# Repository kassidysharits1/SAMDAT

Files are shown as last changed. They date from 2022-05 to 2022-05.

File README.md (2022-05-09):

# SAMDAT


The goal of this project is to create a semi-autonomous magnetics data acquisition tool (SAMDAT). The use of a semi-autonomous vehicle for geophysical data acquisition yields the possibility for quick and efficient surveying. We see rovers being used on other planets, however in the geophysics industry on Earth this is not seen often. This project will aim to create a semi- autonomous tool to collect magnetic data. The goal is for the final product to be relatively low cost and to hopefully have the ability to be used for other geophysical applications with a selection of sensors. 

# Equipment
- Magnetic Fluxgate (https://www.mouser.com/ProductDetail/Texas-Instruments/DRV425EVM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) 
- GPS (https://www.openimpulse.com/blog/products-page/product-category/gy-neo6mv2-gps-module/) 
- Robotics Kits Robot Car Kit-6WD Off-Road Chassis (https://www.electromaker.io/shop/product/robot-car-kit-6wd-off-road-chassis) 
- Arduino Mega 2560 (2) (https://store-usa.arduino.cc/products/arduino-mega-2560-rev3?selectedStore=us)
- Ethernet Shield (https://www.amazon.com/SunFounder-Ethernet-Shield-W5100-Arduino/dp/B00HG82V1A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)
- Micro SD
- Bluetooth (https://makersportal.com/blog/2017/9/20/hm-10-bluetooth-module)
- Motor Driver (2-3) (https://create.arduino.cc/projecthub/ryanchan/how-to-use-the-l298n-motor-driver-b124c5)
- Battery to power car (https://hobbyking.com/en_us/turnigy-5000mah-3s-20c-lipo-pack-xt-90.html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)
- 9V batteries for arduinos 
- Connectors for batteries, arduinos, sensors
- 3D printed magnetometer extender 

# Estimated Cost Analysis:
Below lists the approximated cost of equipment, this parts list assumes buying one sensor as opposed to discounted builk deliveries and does not include tax and shipping. Note that we bought the sensors and arduinos in bulk and therefore our project was a bit less than this cost analysis.
- Robotics Kit: $99.90
- Magnetic Fluxgate: $24
- Arduino Mega: $35.93 (2)
- Ethernet Shield: $20.99
- Micro SD Card: $9
- Motor Driver: $6.99 (3)
- 14.8 V Lithium Ion Battery: $20.89
- 9V batteries: $2 (2)
- GPS Module: $10
- HM10 Bluetooth Module: $10.99

Total: $292.60

# Design
### Robotic Car Kit
Youtube video linked below with a walk through assembly for the 6 WD High Speed Crawler Robot Chassis with Suspension:
https://www.youtube.com/watch?v=SU6XHG54L_c 

Building guide linked below with equipment and build pictures:
https://raw.githubusercontent.com/SeeedDocument/Outsourcing/master/6WD/Robot%20Car%20Kit-6WD%20Off-Road%20Chassis%20Kit%20Guide%20EN%20V1.0.pdf 

### Motor Driver
Note that we are not using a 9V battery, the battery to power the car is being used here.
driver
Figure: Schematic of motor driver

### Magnetic Fluxgate 
Connections: 
- top connection goes to REFOUT
- second connection goes to VOUT
- third connection goes to ground
- fourth connection not used
mag_img
Figure: Magnetic Fluxgate Top View
diagram_mag
Figure: Schematic of Magnetic Fluxgate

### Attaching the magnetometer at a safe distance
Because the robotic car and the arduinos are magnetic, the magnetic fluxgate needs to be suspended a safe distance from this equipment so that it does not pick up these magnetic anomalies and thus recording false anomalies. This was accounted for by 3D-printing a small rod that can be attached to the robotic car platform and extends roughly 5 inches out. We completed some testing with the magnetic fluxgate and the platform and found that magnetic fluxgate reports steady values once it is 5 inches away from the platform. We tested this while running the motor since this does produce a slightly larger anomaly. We decided to give 10 inches for extra measure. 

https://user-images.githubusercontent.com/103535565/163262615-a055875f-b65d-4c38-8e55-ccc3797bc589.MOV

### Bluetooth
hm10

### 3D Printed Magnetometer Extender
The solid works file for this project are attached in this github directory. 

## Compilation
The following diagrams show the wiring diagrams for the driving and data collection systems. Note that the pin connection locations in the diagrams do not align with our project as the diagrams are drawn with an Arduino Uno rather than a Arduino Mega 2560.

### Rover Driving System
Driving System Diagram

### Data Collection System
Data Collection System Diagram

# Test Survey
This video shows the SAMDAT in action in a hallway running over a series of fridge magnets.

https://user-images.githubusercontent.com/104784140/167321360-39053b76-8c38-48cc-887e-6265c37ef1ad.mp4

# Video
Below shows a video of SAMDAT in action on the Colorado School of Mines campus. 

https://user-images.githubusercontent.com/103535565/165623426-cf573f2c-155d-4962-ba4c-ab2bb2be90a3.mov

# Improvements and Potentials
There is large potential with this project to be applied to other geophysical problems using various sensors. By making interchangeable attachments, there is the potential to use other geophysical equipment. The 3D printed rod we attached for the magnetometer is removable and could be replaced with an attached cart that can hold various equipment. 

Specific Recommended improvements:

- Add a surveyor's wheel for better distance precision/accuracy
- Add fifth and sixth wheels to driving system
- Improve weight distribution: the rover currently drives slightly crooked because the weight is not distributed evenly (mainly the heavy battery causing these issues).
- Adaptive driving from GPS information paired with wheel position sensors.
- Waterproofing for all weather conditions.

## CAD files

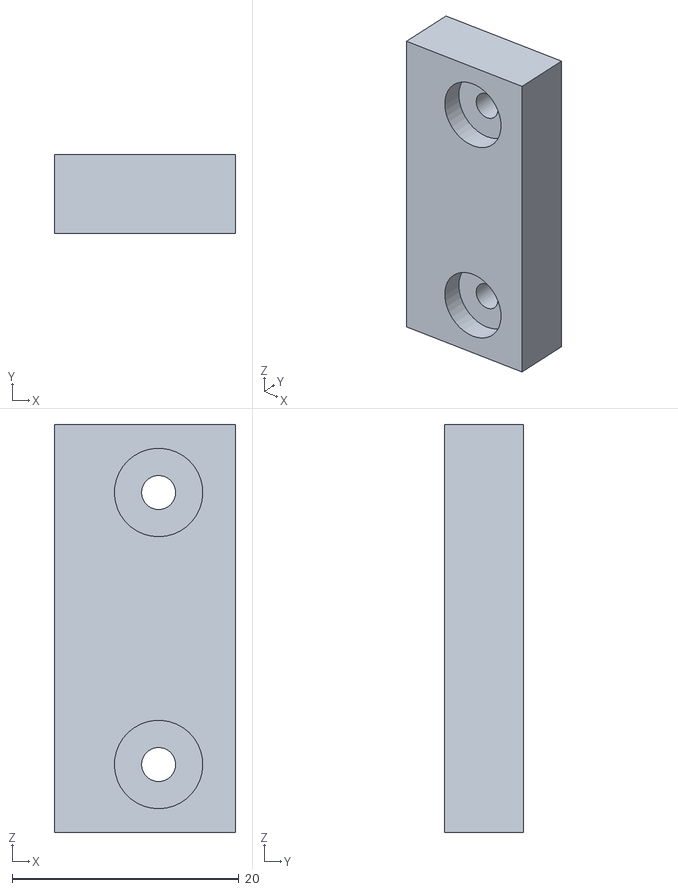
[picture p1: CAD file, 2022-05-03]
bottomclamp.STL
16.0 x 7.00 x 36.0

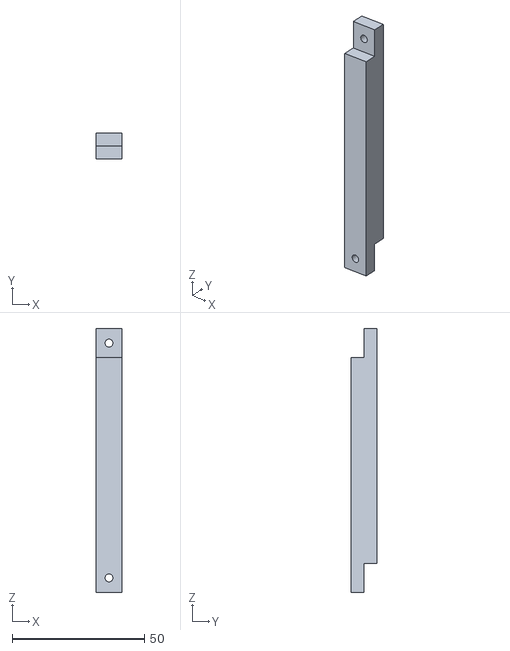
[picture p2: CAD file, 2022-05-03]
arm_10cm.STL
9.80 x 10.0 x 100.0

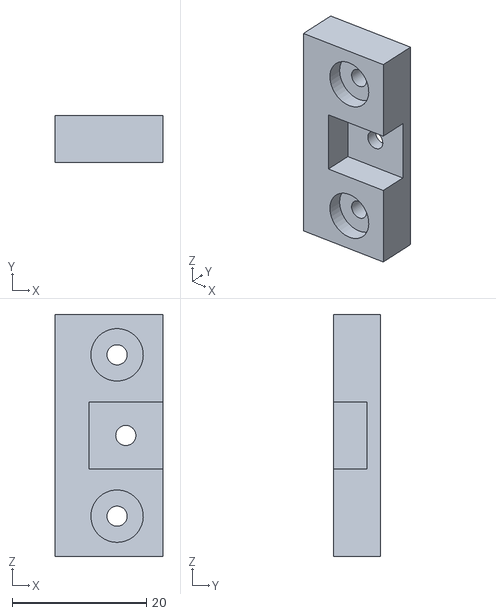
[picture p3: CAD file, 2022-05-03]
topclamp.STL
16.0 x 7.00 x 36.0

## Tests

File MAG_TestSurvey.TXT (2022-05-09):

FieldStrength(nT), Satellites, HDOP, Latitude(deg), Longitude(deg), Fix, Altitude(m), Hour, Minute, Second, Centisecond, day, month, year
----------------------------------------------------------------------------------------------------------------------------------------------
52151.64,0,0,0.00,0.00,4294967295,0.00,0,0,0,0,0,0,2000
52151.64,0,0,0.00,0.00,4294967295,0.00,0,0,0,0,0,0,2000
52049.18,0,9999,0.00,0.00,4294967295,0.00,0,0,0,0,0,0,2000
52151.64,0,9999,0.00,0.00,4294967295,0.00,0,0,0,0,0,0,2000
52049.18,0,9999,0.00,0.00,4294967295,0.00,0,0,0,0,0,0,2000
52049.18,0,9999,0.00,0.00,4294967295,0.00,0,0,0,0,0,0,2000
52151.64,0,9999,0.00,0.00,4294967295,0.00,0,0,0,0,0,0,2000
52151.64,0,9999,0.00,0.00,4294967295,0.00,0,0,0,0,0,0,2000
52151.64,0,9999,0.00,0.00,4294967295,0.00,0,0,0,0,0,0,2000
52151.64,0,9999,0.00,0.00,4294967295,0.00,0,0,0,0,0,0,2000
52151.64,0,9999,0.00,0.00,4294967295,0.00,0,0,0,0,0,0,2000
52049.18,0,9999,0.00,0.00,4294967295,0.00,0,0,0,0,0,0,2000
52049.18,0,9999,0.00,0.00,4294967295,0.00,0,0,0,0,0,0,2000
52049.18,0,9999,0.00,0.00,4294967295,0.00,0,0,0,0,0,0,2000
52151.64,0,9999,0.00,0.00,4294967295,0.00,0,0,0,0,0,0,2000
52151.64,0,9999,0.00,0.00,4294967295,0.00,0,0,0,0,0,0,2000
52151.64,0,9999,0.00,0.00,4294967295,0.00,0,0,0,0,0,0,2000
52151.64,0,9999,0.00,0.00,4294967295,0.00,0,0,0,0,0,0,2000
52151.64,0,9999,0.00,0.00,4294967295,0.00,0,0,0,0,0,0,2000
52151.64,0,9999,0.00,0.00,4294967295,0.00,0,0,0,0,0,0,2000
52151.64,0,9999,0.00,0.00,4294967295,0.00,0,0,0,0,0,0,2000
52049.18,0,9999,0.00,0.00,4294967295,0.00,0,0,0,0,0,0,2000
52254.10,0,9999,0.00,0.00,4294967295,0.00,0,0,0,0,0,0,2000
52049.18,0,9999,0.00,0.00,4294967295,0.00,0,0,0,0,0,0,2000
52151.64,0,9999,0.00,0.00,4294967295,0.00,0,0,0,0,0,0,2000
52356.55,0,9999,0.00,0.00,4294967295,0.00,0,0,0,0,0,0,2000
52459.01,0,9999,0.00,0.00,4294967295,0.00,0,0,0,0,0,0,2000
52561.48,0,9999,0.00,0.00,4294967295,0.00,0,0,0,0,0,0,2000
52561.48,0,9999,0.00,0.00,4294967295,0.00,0,0,0,0,0,0,2000
52459.01,0,9999,0.00,0.00,4294967295,0.00,0,0,0,0,0,0,2000
52356.55,0,9999,0.00,0.00,4294967295,0.00,0,0,0,0,0,0,2000
52356.55,0,9999,0.00,0.00,4294967295,0.00,0,0,0,0,0,0,2000
52356.55,0,9999,0.00,0.00,4294967295,0.00,0,0,0,0,0,0,2000
52356.55,0,9999,0.00,0.00,4294967295,0.00,0,0,0,0,0,0,2000
52561.48,0,9999,0.00,0.00,4294967295,0.00,0,0,0,0,0,0,2000
52356.55,0,9999,0.00,0.00,4294967295,0.00,0,0,0,0,0,0,2000
52356.55,0,9999,0.00,0.00,4294967295,0.00,0,0,0,0,0,0,2000
52356.55,0,9999,0.00,0.00,4294967295,0.00,0,0,0,0,0,0,2000
52356.55,0,9999,0.00,0.00,4294967295,0.00,0,0,0,0,0,0,2000
52459.01,0,9999,0.00,0.00,4294967295,0.00,0,0,0,0,0,0,2000
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

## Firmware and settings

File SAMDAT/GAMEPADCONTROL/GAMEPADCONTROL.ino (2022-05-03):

#define CUSTOM_SETTINGS
#define INCLUDE_GAMEPAD_MODULE
#include <Dabble.h>


char data;

// Back motors
int motor1pin1 = 24;
int motor1pin2 = 26;
int motor2pin1 = 28;
int motor2pin2 = 30;

int ENA1 = 6;
int ENB1 = 5;


// Back motors

int motor3pin1 = 32;
int motor3pin2 = 34;
int motor4pin1 = 36;
int motor4pin2 = 38;

int ENA2 = 10;
int ENB2 = 9;


//Speed
int grass = 100;
int grassTurn = 250;
int inside = 40;
int insideTurn = 250;

int lineLen = 5000;
int turnLen = 680;
int stopLen = 1000;


void setup() {
  Serial.begin(9600);
  Serial3.begin(9600);
  Dabble.begin(Serial3);
  
  // put your setup code here, to run once:
  pinMode(motor1pin1, OUTPUT);
  pinMode(motor1pin2, OUTPUT);
  pinMode(motor2pin1, OUTPUT);
  pinMode(motor2pin2, OUTPUT);

  pinMode(motor3pin1, OUTPUT);
  pinMode(motor3pin2, OUTPUT);
  pinMode(motor4pin1, OUTPUT);
  pinMode(motor4pin2, OUTPUT);
  
  pinMode(ENA1, OUTPUT); 
  pinMode(ENB1, OUTPUT);
  pinMode(ENA2, OUTPUT); 
  pinMode(ENB2, OUTPUT);
}

void loop() {
  // put your main code here, to run repeatedly:   
  Dabble.processInput();  // This line is crucial in grabbing our data  
  
  while (GamePad.isUpPressed()) {
    Serial.println("Forward");
    analogWrite(ENA1, inside);
    analogWrite(ENB1, inside);
    analogWrite(ENA2, inside);
    analogWrite(ENB2, inside);
  
    digitalWrite(motor1pin1, HIGH);
    digitalWrite(motor1pin2, LOW);
    digitalWrite(motor3pin1, HIGH);
    digitalWrite(motor3pin2, LOW);
  
    digitalWrite(motor2pin1, HIGH);
    digitalWrite(motor2pin2, LOW);
    digitalWrite(motor4pin1, HIGH);
    digitalWrite(motor4pin2, LOW);

    Dabble.processInput();
  }
  
  while (GamePad.isDownPressed()) {
    Serial.println("Backwards");
    analogWrite(ENA1, inside);
    analogWrite(ENB1, inside);
    analogWrite(ENA2, inside);
    analogWrite(ENB2, inside);
    
    digitalWrite(motor1pin1, LOW);
    digitalWrite(motor1pin2, HIGH);
    digitalWrite(motor3pin1, LOW);
    digitalWrite(motor3pin2, HIGH);
  
    digitalWrite(motor2pin1, LOW);
    digitalWrite(motor2pin2, HIGH);
    digitalWrite(motor4pin1, LOW);
    digitalWrite(motor4pin2, HIGH);

    Dabble.processInput();
  }

  while (GamePad.isLeftPressed())
  {
    Serial.print("Left");
    analogWrite(ENA1, insideTurn);
    analogWrite(ENB1, insideTurn);
    analogWrite(ENA2, insideTurn);
    analogWrite(ENB2, insideTurn);
    
    digitalWrite(motor2pin1, LOW);
    digitalWrite(motor2pin2, HIGH);
    
    digitalWrite(motor3pin1, HIGH);
    digitalWrite(motor3pin2, LOW);
    digitalWrite(motor4pin1, LOW);
    digitalWrite(motor4pin2, HIGH);

    Dabble.processInput();
  }

  while (GamePad.isRightPressed())
  {
    Serial.print("Right");
    analogWrite(ENA1, insideTurn);
    analogWrite(ENB1, insideTurn);
    analogWrite(ENA2, insideTurn);
    analogWrite(ENB2, insideTurn);
    
    digitalWrite(motor1pin1, LOW);
    digitalWrite(motor1pin2, HIGH);
    
    digitalWrite(motor3pin1, LOW);
    digitalWrite(motor3pin2, HIGH);
    digitalWrite(motor4pin1, HIGH);
    digitalWrite(motor4pin2, LOW);

    Dabble.processInput();
  }

  while (GamePad.isSquarePressed())
  {
    Serial.println("Square");
  }

  while (GamePad.isCirclePressed())
  {
    Serial.println("Circle");
    Dabble.processInput();
  }

  while (GamePad.isCrossPressed())
  {
    Serial.print("Cross");
  }

  while (GamePad.isTrianglePressed())
  {
    Serial.print("Triangle");
  }

  while (GamePad.isSelectPressed())
  {
    Serial.print("Start");
  }

  if (GamePad.isStartPressed())
  {
    Serial.println("Select");
    Serial.println("Starting Suvey");
    
    int i = 0;
    while (i < 4) {
      //Forward
      Serial.println("i");
      analogWrite(ENA1, inside); //ENA pin
      analogWrite(ENB1, inside); //ENB pin
      analogWrite(ENA2, inside); //ENA pin
      analogWrite(ENB2, inside); //ENB pin
      delay(stopLen);
      
      digitalWrite(motor1pin1, HIGH);
      digitalWrite(motor1pin2, LOW);
      digitalWrite(motor3pin1, HIGH);
      digitalWrite(motor3pin2, LOW);
    
      digitalWrite(motor2pin1, HIGH);
      digitalWrite(motor2pin2, LOW);
      digitalWrite(motor4pin1, HIGH);
      digitalWrite(motor4pin2, LOW);
      delay(lineLen);
      
      //Stop
      digitalWrite(motor1pin1, LOW);
      digitalWrite(motor1pin2, LOW);
      digitalWrite(motor3pin1, LOW);
      digitalWrite(motor3pin2, LOW);
      digitalWrite(motor2pin1, LOW);
      digitalWrite(motor2pin2, LOW);
      digitalWrite(motor4pin1, LOW);
      digitalWrite(motor4pin2, LOW);
      delay(stopLen);
      
      //Turn left
      analogWrite(ENA1, insideTurn); //ENA pin
      analogWrite(ENB1, insideTurn); //ENB pin
      analogWrite(ENA2, insideTurn); //ENA pin
      analogWrite(ENB2, insideTurn); //ENB pin
      delay(stopLen);
      
      //digitalWrite(motor1pin1, HIGH);
      //digitalWrite(motor1pin2, LOW);
      digitalWrite(motor2pin1, LOW);
      digitalWrite(motor2pin2, HIGH);
      
      digitalWrite(motor3pin1, HIGH);
      digitalWrite(motor3pin2, LOW);
      digitalWrite(motor4pin1, LOW);
      digitalWrite(motor4pin2, HIGH);
      delay(turnLen);
    
      //Stop
      digitalWrite(motor1pin1, LOW);
      digitalWrite(motor1pin2, LOW);
      digitalWrite(motor3pin1, LOW);
      digitalWrite(motor3pin2, LOW);
      digitalWrite(motor2pin1, LOW);
      digitalWrite(motor2pin2, LOW);
      digitalWrite(motor4pin1, LOW);
      digitalWrite(motor4pin2, LOW);
      delay(stopLen);

      i = i+1;
    }


  
    Dabble.processInput();
  }
  else {
    Serial.println("Stop");
    
    digitalWrite(motor1pin1, LOW);
    digitalWrite(motor1pin2, LOW);
    digitalWrite(motor2pin1, LOW);
    digitalWrite(motor2pin2, LOW);
    
    digitalWrite(motor3pin1, LOW);
    digitalWrite(motor3pin2, LOW);
    digitalWrite(motor4pin1, LOW);
    digitalWrite(motor4pin2, LOW);
  }
}


void Survey(int i) {
  for (int i = 0; i++; i<4) {
    //Forward
    analogWrite(ENA1, inside); //ENA pin
    analogWrite(ENB1, inside); //ENB pin
    analogWrite(ENA2, inside); //ENA pin
    analogWrite(ENB2, inside); //ENB pin
    delay(stopLen);
    
    digitalWrite(motor1pin1, HIGH);
    digitalWrite(motor1pin2, LOW);
    digitalWrite(motor3pin1, HIGH);
    digitalWrite(motor3pin2, LOW);
  
    digitalWrite(motor2pin1, HIGH);
    digitalWrite(motor2pin2, LOW);
    digitalWrite(motor4pin1, HIGH);
    digitalWrite(motor4pin2, LOW);
    delay(lineLen);
    
    //Stop
    digitalWrite(motor1pin1, LOW);
    digitalWrite(motor1pin2, LOW);
    digitalWrite(motor3pin1, LOW);
    digitalWrite(motor3pin2, LOW);
    digitalWrite(motor2pin1, LOW);
    digitalWrite(motor2pin2, LOW);
    digitalWrite(motor4pin1, LOW);
    digitalWrite(motor4pin2, LOW);
    delay(stopLen);
    
    //Turn left
    analogWrite(ENA1, insideTurn); //ENA pin
    analogWrite(ENB1, insideTurn); //ENB pin
    analogWrite(ENA2, insideTurn); //ENA pin
    analogWrite(ENB2, insideTurn); //ENB pin
    delay(stopLen);
    
    //digitalWrite(motor1pin1, HIGH);
    //digitalWrite(motor1pin2, LOW);
    digitalWrite(motor2pin1, LOW);
    digitalWrite(motor2pin2, HIGH);
    
    digitalWrite(motor3pin1, HIGH);
    digitalWrite(motor3pin2, LOW);
    digitalWrite(motor4pin1, LOW);
    digitalWrite(motor4pin2, HIGH);
    delay(turnLen);
  
    //Stop
    digitalWrite(motor1pin1, LOW);
    digitalWrite(motor1pin2, LOW);
    digitalWrite(motor3pin1, LOW);
    digitalWrite(motor3pin2, LOW);
    digitalWrite(motor2pin1, LOW);
    digitalWrite(motor2pin2, LOW);
    digitalWrite(motor4pin1, LOW);
    digitalWrite(motor4pin2, LOW);
    delay(stopLen);
  }
}

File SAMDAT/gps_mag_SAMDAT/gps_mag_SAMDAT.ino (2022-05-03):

#include <TinyGPS++.h>
#include <SoftwareSerial.h>
#include <SD.h>

static const int RXPin = 11, TXPin = 9;
static const uint32_t GPSBaud = 9600;

const int dataPin = A0, chipSelect = 53;
float V_out = 0, R1 = 100, B = 0;

float latt = 0, lon = 0; 
int mm = 0, dd = 0, yy = 0, h = 0, m = 0, s = 0, cs = 0, ii;


// The TinyGPS++ object
TinyGPSPlus gps;

// The serial connection to the GPS device
SoftwareSerial ss(RXPin, TXPin);


// Set-up
void setup()
{
  // Initialize serial monitor
  Serial.begin(9600); 
  
  // Initialize serial conneciton to GPS
  ss.begin(GPSBaud);

  // Initialize SD card
  Serial.println("Initializing SD card...");
  pinMode(chipSelect, HIGH);
  
  // check that the memory card exists and is usable
  if (!SD.begin(chipSelect))
  {
    Serial.println("Card failed, or not present");
    // stop sketch
    return;
  }
  Serial.println("memory card is ready");
  if (SD.exists("mag.TXT")) 
  {
    SD.remove("mag.TXT");
  }


  Serial.println(F("Sats HDOP Latitude   Longitude   Fix  Date       Time     Date Alt    Course Speed Card  Distance Course Card  Chars Sentences Checksum"));
  Serial.println(F("          (deg)      (deg)       Age                      Age  (m)    --- from GPS ----  ---- to London  ----  RX    RX        Fail"));
  Serial.println(F("---------------------------------------------------------------------------------------------------------------------------------------"));
  
  File dataFile = SD.open("mag.TXT", FILE_WRITE);

  if (dataFile) {
    dataFile.println(F("FieldStrength(nT), Satellites, HDOP, Latitude(deg), Longitude(deg), Fix, Altitude(m), Hour, Minute, Second, Centisecond, day, month, year"));
    dataFile.println(F("----------------------------------------------------------------------------------------------------------------------------------------------"));
    dataFile.close();
  }
}


// Methods for magnetometer and GPS
float getMag()
{
  V_out = analogRead(dataPin);   // read the input pin
  B = V_out / (8*12.2*R1); // mT
  B = B*pow(10,6);

  return B;
}

static void smartDelay(unsigned long ms)
{
  unsigned long start = millis();
  do 
  {
    while (ss.available())
      gps.encode(ss.read());
  } while (millis() - start < ms);
}

static void printInt(unsigned long val, bool valid, int len)
{
  char sz[32] = "*****************";
  if (valid)
    sprintf(sz, "%ld", val);
  sz[len] = 0;
  for (int i=strlen(sz); i<len; ++i)
    sz[i] = ' ';
  if (len > 0) 
    sz[len-1] = ' ';
  Serial.print(sz);
  smartDelay(0);
}

static void printFloat(float val, bool valid, int len, int prec)
{
  if (!valid)
  {
    while (len-- > 1)
      Serial.print('*');
    Serial.print(' ');
  }
  else
  {
    Serial.print(val, prec);
    int vi = abs((int)val);
    int flen = prec + (val < 0.0 ? 2 : 1); // . and -
    flen += vi >= 1000 ? 4 : vi >= 100 ? 3 : vi >= 10 ? 2 : 1;
    for (int i=flen; i<len; ++i)
      Serial.print(' ');
  }
  smartDelay(0);
}

static void printDateTime(TinyGPSDate &d, TinyGPSTime &t)
{
  if (!d.isValid())
  {
    Serial.print(F("********** "));
  }
  else
  {
    char sz[32];
    sprintf(sz, "%02d/%02d/%02d ", d.month(), d.day(), d.year());
    Serial.print(sz);
  }
  
  if (!t.isValid())
  {
    Serial.print(F("******** "));
  }
  else
  {
    char sz[32];
    sprintf(sz, "%02d:%02d:%02d ", t.hour(), t.minute(), t.second());
    Serial.print(sz);
  }

  printInt(d.age(), d.isValid(), 5);
  smartDelay(0);
}

static void printStr(const char *str, int len)
{
  int slen = strlen(str);
  for (int i=0; i<len; ++i)
    Serial.print(i<slen ? str[i] : ' ');
  smartDelay(0);
}

/////////////////////////////////////////////////////////
void loop()
{
  static const double LONDON_LAT = 51.508131, LONDON_LON = -0.128002;

  printInt(gps.satellites.value(), gps.satellites.isValid(), 5);
  printInt(gps.hdop.value(), gps.hdop.isValid(), 5);
  printFloat(gps.location.lat(), gps.location.isValid(), 11, 6);
  printFloat(gps.location.lng(), gps.location.isValid(), 12, 6);
  printInt(gps.location.age(), gps.location.isValid(), 5);
  printDateTime(gps.date, gps.time);
  printFloat(gps.altitude.meters(), gps.altitude.isValid(), 7, 2);
  printFloat(gps.course.deg(), gps.course.isValid(), 7, 2);
  printFloat(gps.speed.kmph(), gps.speed.isValid(), 6, 2);
  printStr(gps.course.isValid() ? TinyGPSPlus::cardinal(gps.course.value()) : "*** ", 6);

  unsigned long distanceKmToLondon =
    (unsigned long)TinyGPSPlus::distanceBetween(
      gps.location.lat(),
      gps.location.lng(),
      LONDON_LAT, 
      LONDON_LON) / 1000;
  printInt(distanceKmToLondon, gps.location.isValid(), 9);

  double courseToLondon =
    TinyGPSPlus::courseTo(
      gps.location.lat(),
      gps.location.lng(),
      LONDON_LAT, 
      LONDON_LON);

  printFloat(courseToLondon, gps.location.isValid(), 7, 2);

  const char *cardinalToLondon = TinyGPSPlus::cardinal(courseToLondon);
  
  printStr(gps.location.isValid() ? cardinalToLondon : "*** ", 6);
  
  printInt(gps.charsProcessed(), true, 6);
  printInt(gps.sentencesWithFix(), true, 10);
  printInt(gps.failedChecksum(), true, 9);
  Serial.println();
    
  File dataFile = SD.open("MAG.TXT", FILE_WRITE);
  
  if (dataFile) 
  {
      dataFile.print(getMag());
      dataFile.print(F(","));
      dataFile.print(gps.satellites.value());
      dataFile.print(F(","));
      dataFile.print(gps.hdop.value());
      dataFile.print(F(","));
      dataFile.print(gps.location.lat());
      dataFile.print(F(","));
      dataFile.print(gps.location.lng());
      dataFile.print(F(","));
      dataFile.print(gps.location.age());
      dataFile.print(F(","));
      dataFile.print(gps.altitude.meters());
      dataFile.print(F(","));
      dataFile.print(gps.time.hour());
      dataFile.print(F(","));
      dataFile.print(gps.time.minute());
      dataFile.print(F(","));
      dataFile.print(gps.time.second());
      dataFile.print(F(","));
      dataFile.print(gps.time.centisecond());
      dataFile.print(F(","));
      dataFile.print(gps.date.day());
      dataFile.print(F(","));
      dataFile.print(gps.date.month());
      dataFile.print(F(","));
      dataFile.print(gps.date.year());
      dataFile.println();
      dataFile.close();
  }

  smartDelay(250);

  if (millis() > 5000 && gps.charsProcessed() < 10) {
    Serial.println(F("No GPS data received: check wiring"));
  }
    
}
